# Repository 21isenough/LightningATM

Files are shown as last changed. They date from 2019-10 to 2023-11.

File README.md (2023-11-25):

# LightningATM

### 🔥🔥🔥 Now a seconde funding source next to LNbits is available. 🔥🔥🔥
### 👉👉👉 [blink.sv](https://www.blink.sv/) 🔥 See how to update: [Update](/docs/guide/perform_update.md) 👈👈👈

This LightningATM was built to distribute small amounts of BTC - obviously - it only accepts coins. It shall demonstrate the power of Bitcoins Lightning Network. A two cent coin is enough to buy some satoshis at the LightningATM.

A physical coin exchanged into bitcoin and send to your lightning wallet in seconds. Use this project to educate your family and friends or guests at your bitcoin meetup - a convenient and easy on-boarding process for people that are new to bitcoin.

**Please be aware that this is a hobbyist project and it is not secure and reliable enough to withstand attacks. I discourage the use of this setup in a professional environment - but it's rather a good educational tool**

There are currently two versions of the Lightning ATM. The large full version with a camera for scanning invoices and a button for acknowledgment and other functions. And there is the somewhat slimmed-down version for mobile use, the pocket version.

Full Version             |  Pocket Version
:-------------------------:|:-------------------------:
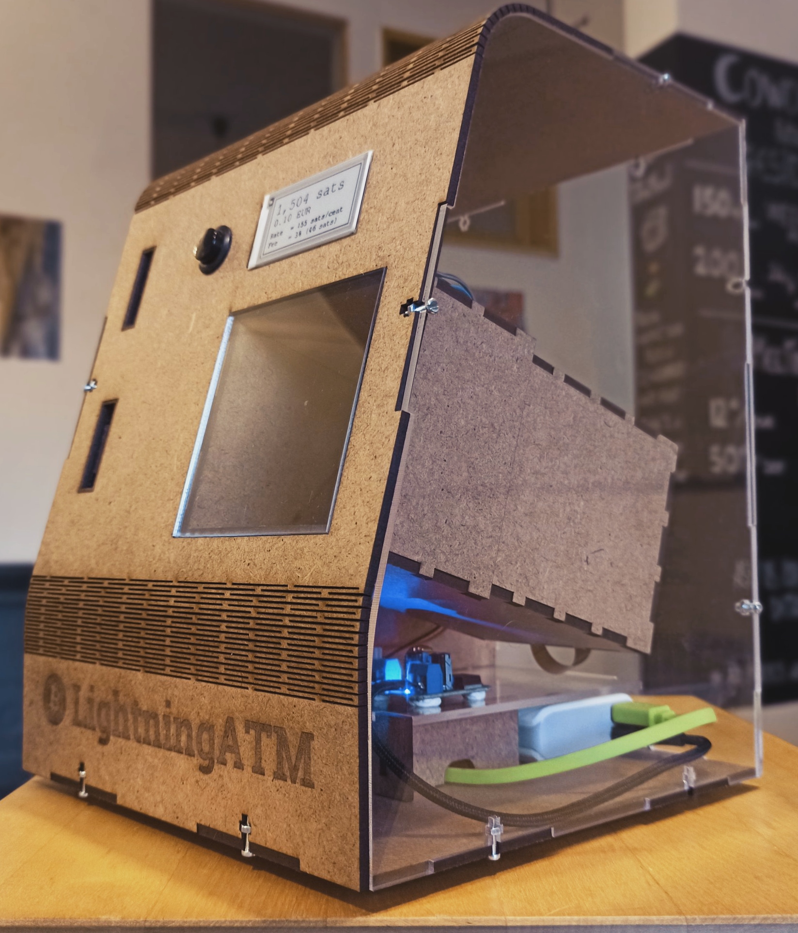
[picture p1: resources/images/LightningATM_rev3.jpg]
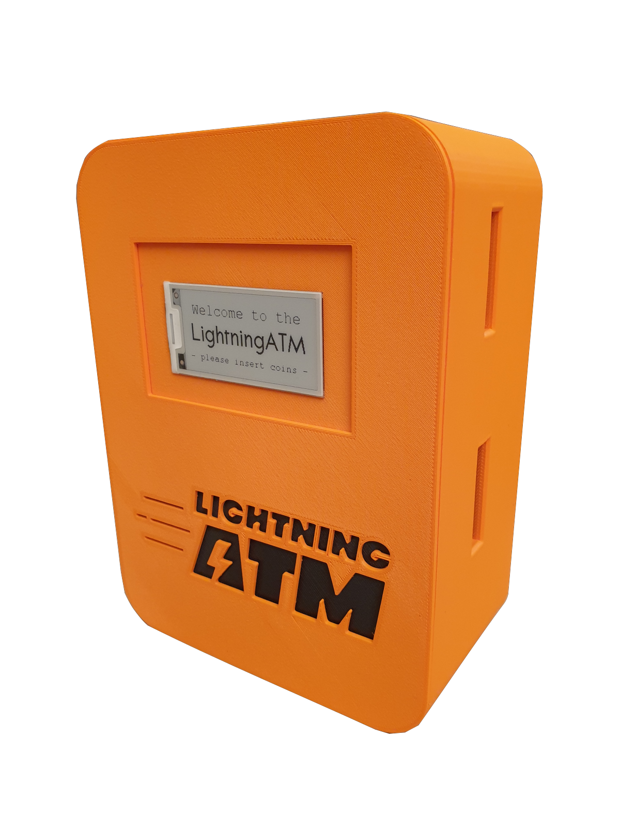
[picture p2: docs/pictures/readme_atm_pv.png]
  |  

### Required components

- [parts list](/docs/guide/parts_list.md)

### Installation guideline

_Carry out the points step by step as described here. This is the quickest way to succeed._ 😊

- [voltage converter](/docs/guide/voltage_converter.md)
- [coin validator](/docs/guide/coin_validator.md)
- [wiring](/docs/guide/wiring.md)
- [sd card and wifi](/docs/guide/sdcard_and_wifi.md)
- [display](/docs/guide/display.md)
- [edit config.ini](/docs/guide/edit_config.md)
- [debugging and tmux](/docs/guide/tmux_monitoring.md)
- [autostart](/docs/guide/autostart.md)
- [aditional information and tips](/docs/guide/information_and_tips.md)
- [option: language](/docs/guide/languages.md) 
- [option: button](/docs/guide/button.md)
- [option: camera](/docs/guide/camera.md)
- [option: lockout relay](/docs/guide/relay.md)
- [option: RPi image from scratch](/docs/guide/rpi_image_from_scratch.md)

If you want to update your ATM with LNbits, see this guide: [Update](/docs/guide/perform_update.md)

More information of how to setup the LightningATM can be found here https://docs.lightningatm.me. Also join the Telegram group of LightningATM builders here https://t.me/lightningatm_building or contact 21isenough on Twitter (https://twitter.com/21isenough).

To see the Lightning ATM in action, check out this video [LightningATM in action](https://twitter.com/21isenough/status/1170808396955738114?s=20)

### Mentioned
- https://podcasts.apple.com/us/podcast/interview-with-21isenough/id1481514734?i=1000458712983
- https://blog.sicksubroutine.com/lightning-junkies-episode-021/
- http://bitcoin-turm.de/bturm29/
- https://www.atmmarketplace.com/articles/lightning-atm-lets-you-buy-itty-bitty-amounts-of-bitcoin/
- https://www.bitcoinmedia.id/atm-bitcoin-lightning-ini-adalah-prototype-pertama/
- https://twitter.com/CoinATMRadar/status/1202657309765357568?s=20
- https://www.hackster.io/news/lightningatm-distributes-small-amounts-of-btc-over-the-lightning-network-5e03347acd88
- https://criptonizando.com/2019/10/08/desenvolvedor-cria-caixa-eletronico-de-bitcoin-que-ate-amadores-podem-construir-usando-a-lightning-network/
- https://decrypt.co/10046/ightningatm-how-to-make-your-own-bitcoin-atm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

### Documentations in other languages

- German Video: [Tutorial - Bitcoin Lightning ATM - montieren und konfigurieren](https://www.youtube.com/watch?v=pTyTc2qPQj0)
- German tutorial for the pocket edition: [Tutorial LightningATM - ereignishorizont.xyz](https://ereignishorizont.xyz/lightning-atm/)

### Todo list

#### Prio 1
- [ ] Implement lndconnect
- [ ] Add "no wallet setup" warning at boot
- [ ] Implement LNURLProxyAPI
- [ ] Support for more Lightning implementations and wallets
- [ ] Try different way of detecting inserted coins (populating a list and setting a delimiter)
- [ ] PCB Board design (https://easyeda.com/, http://kicad.org/)
- [ ] 5V-12V step up transformer (http://www.electronics-lab.com/project/5v-to-12v-step-up-dc-dc-converter/)
- [ ] Solve security concerns in regards to lnurl (scan over the shoulder)
#### Prio 2
- [ ] Dashboard for settings (via mobile)
- [ ] Add second button and admin menu
- [ ] Add admin function only available through qr pass
- [ ] Run certain functions in threads
- [ ] Additional button for restart and shutdown
- [ ] Find solution to work without jumper cables
- [ ] Add encrypted partition with sensible data
#### Prio 3
- [ ] Add TOR support for LND calls
- [ ] Store data in database
- [ ] Add AP option for users to login into their wifis (https://github.com/21isenough/RaspiWiFi)
- [ ] 2 layer for coins to reject before accepted
#### Done
- [X] Update doc with new features, screens
- [X] Check out BTCPay API to integrate backend
- [X] Add coin return stopper to 3d design
- [X] Try different e-ink screen
- [X] Add a language file to change strings easily
- [X] Write installations instructions (see docs.lightningatm.me)
- [X] Rethink the design decisions in regards to hardware (https://www.arrow.com/en/products)
- [X] Add encryption of admin.macaroon in idle mode
- [X] Design ideas for case
- [X] Slightly recline front board to the back, add immersion for camera
- [X] Move scanning function into utils
- [X] Move all display functions into display.py
- [X] Implement lnurl with lntxbot
- [X] Draw printer and boards in 3D (https://www.onshape.com/)
- [X] Write list of all compatible wallets/qr qr_codes
- [X] Test qr code on 2" eInk display (works)
- [X] Research camera resolutions / qr code scanning
- [X] Check if there's other zbar python libraries
- [X] Change to wide angle camera
- [X] Sort out scan errors
- [x] QR code scan function
- [x] Validate requested amount
- [x] Reject to high amounts
- [x] Add config file
- [x] Add parts list to readme
- [x] Ask for rescan of QR code
- [x] Inform about failed scan
- [x] Implement continuous QR Scan
- [x] Lower case ln invoices
- [x] Find a faster solution for QR scans (zbarcam)
- [x] Organize todos better

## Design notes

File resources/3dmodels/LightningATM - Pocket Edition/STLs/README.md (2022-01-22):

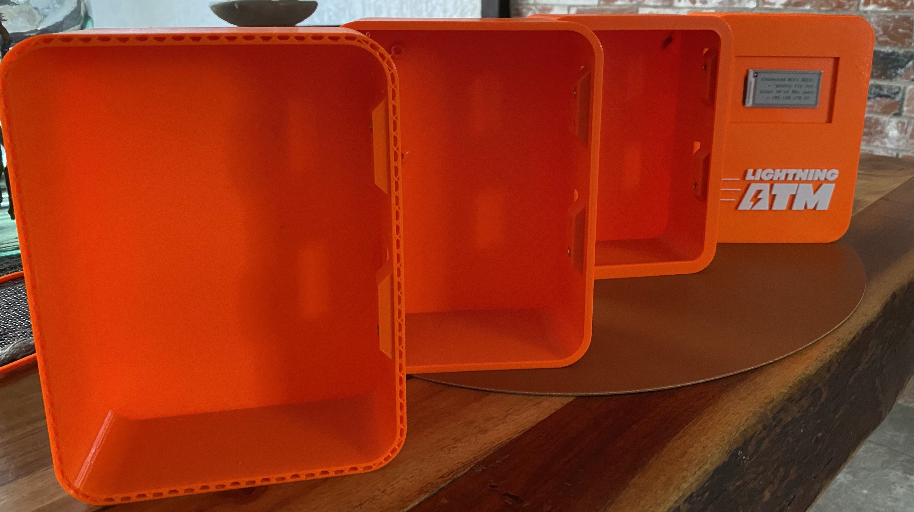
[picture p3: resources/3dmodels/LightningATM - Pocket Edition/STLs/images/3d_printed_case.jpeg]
 <br>

# 3D Printed L-ATM Case PE-Edition

Below files can be used to print a case, which lowers your overall costs. The models can be printed  without any supports.

This is the first version and is designed to be used with inserts to mount the Coin-Acceptor as well as the Rasbperry-Pi Zero. For the Coin Acceptor use **M3** inserts [(Amazon)](https://amzn.to/35eNkgj), for the Raspberry-Pi **M2.5** [(Amazon)](https://amzn.to/2HjF0Uo) inserts are needed.
The Lids holds by friction fit.

For the case **needed** are 3 Parts: 
- **Shell**
  
- **Back Lid**
  - two versions
    - normal with 2mm thick plate
    - thicker with 3mm thick plate
- **Top Lid**
  - there are two separate versions:
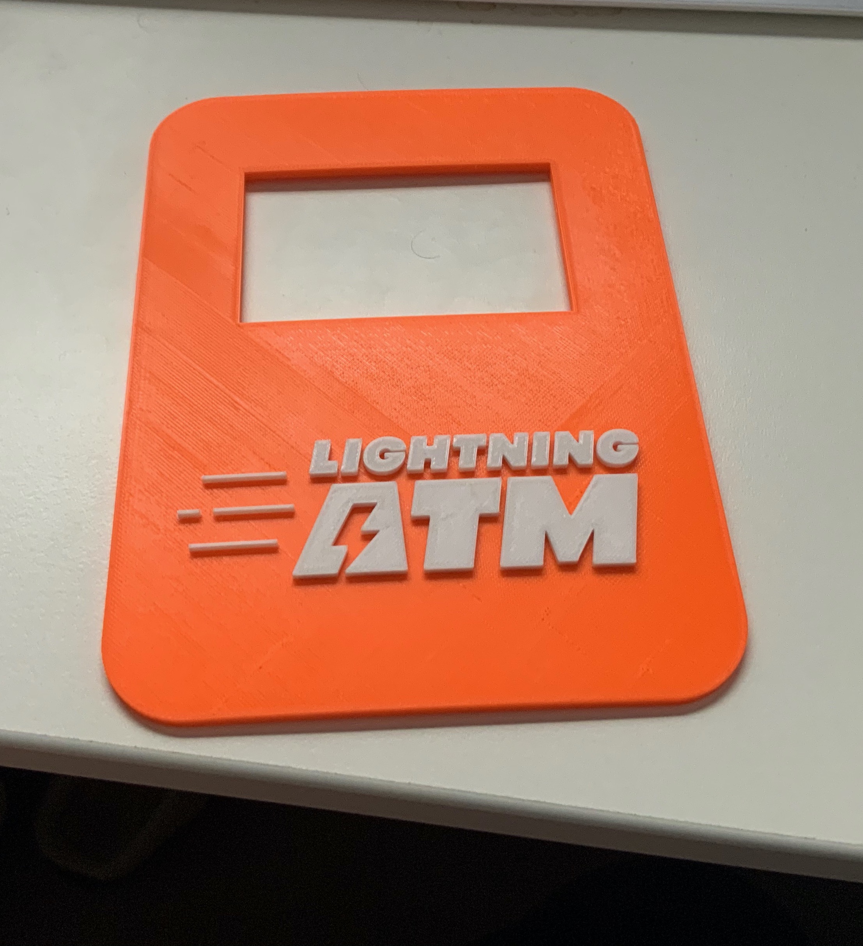
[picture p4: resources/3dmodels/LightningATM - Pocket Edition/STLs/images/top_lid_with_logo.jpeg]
    - with Lightning-Logo, *for dual color print add a **color change at Z 3.00 mm***. 
    - without any logo
- Mounting Rim
  - optional but *recommended* to properly glue the Top Lid onto the Back Lid.

1. Print Shell / Back Lid / Top Lid / Mounting Rim
2. Use soldering iron to:
   1. Add M3 Inserts into Coin Acceptor holes 
   2. Add M2.5 Inserts into Raspberry holes
   
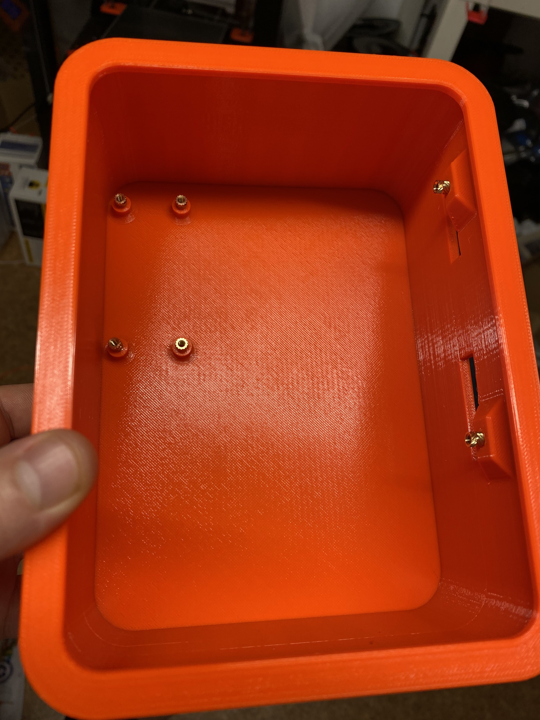
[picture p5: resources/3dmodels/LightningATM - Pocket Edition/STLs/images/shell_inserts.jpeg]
   <br> <br>
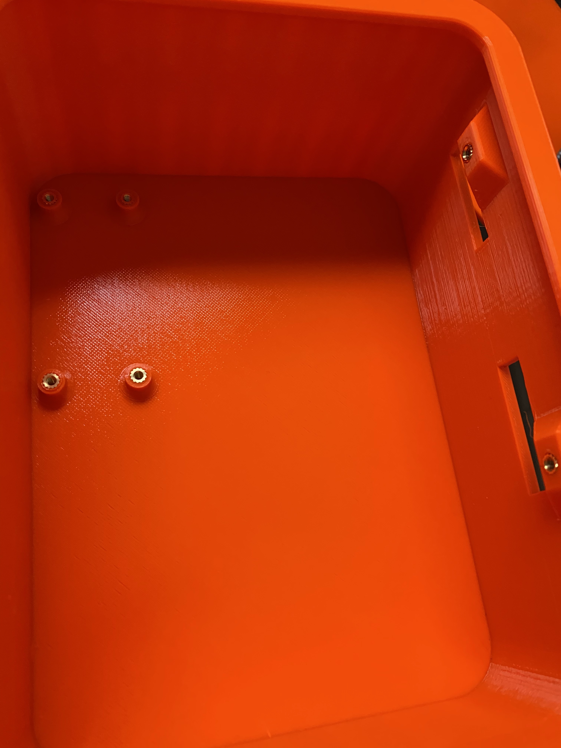
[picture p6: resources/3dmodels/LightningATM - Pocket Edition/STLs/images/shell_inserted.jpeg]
   
   
3. If you have printed the *Mounting Rim* put it around the BackLid
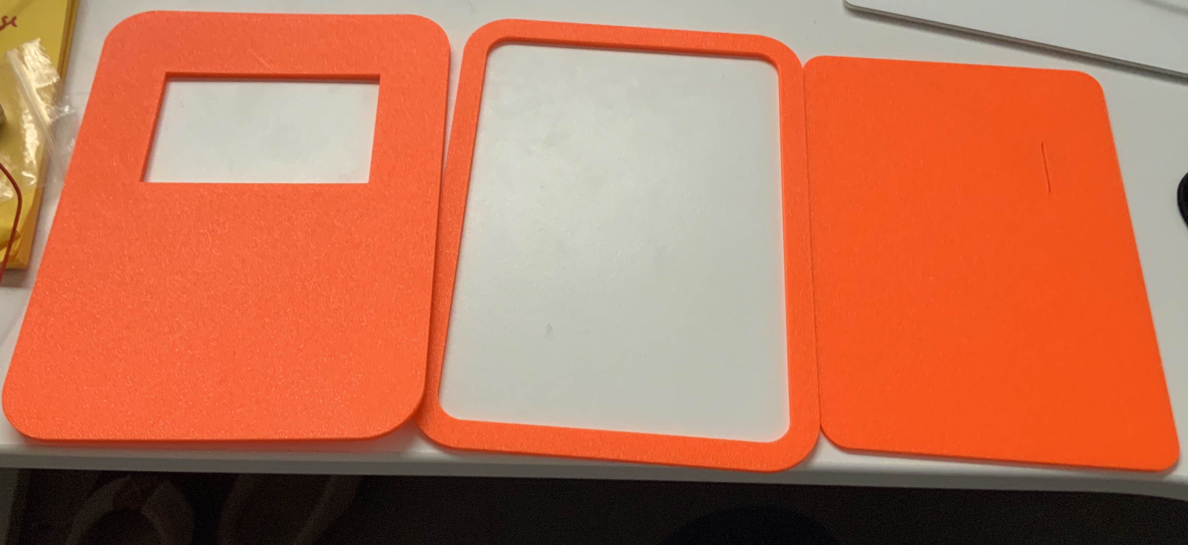
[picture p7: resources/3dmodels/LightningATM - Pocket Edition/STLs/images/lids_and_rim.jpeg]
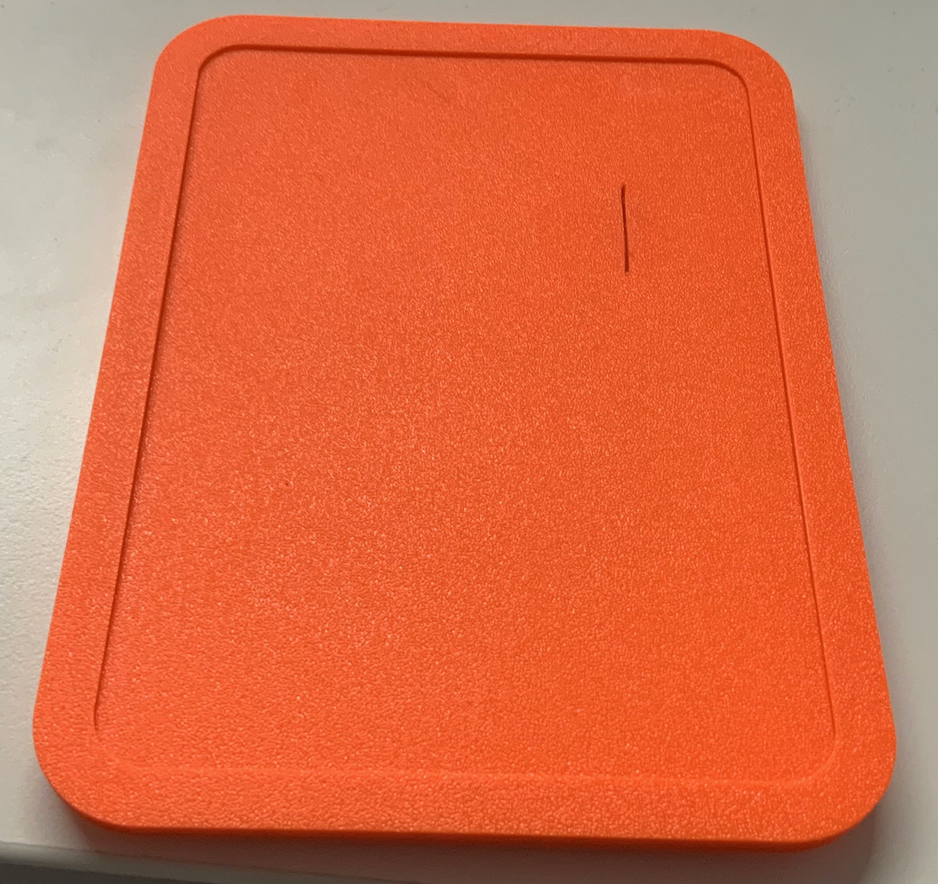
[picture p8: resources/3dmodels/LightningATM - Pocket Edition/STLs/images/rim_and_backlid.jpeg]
<br> <br> 
4. put glue on the Top Lid and use something to press both together
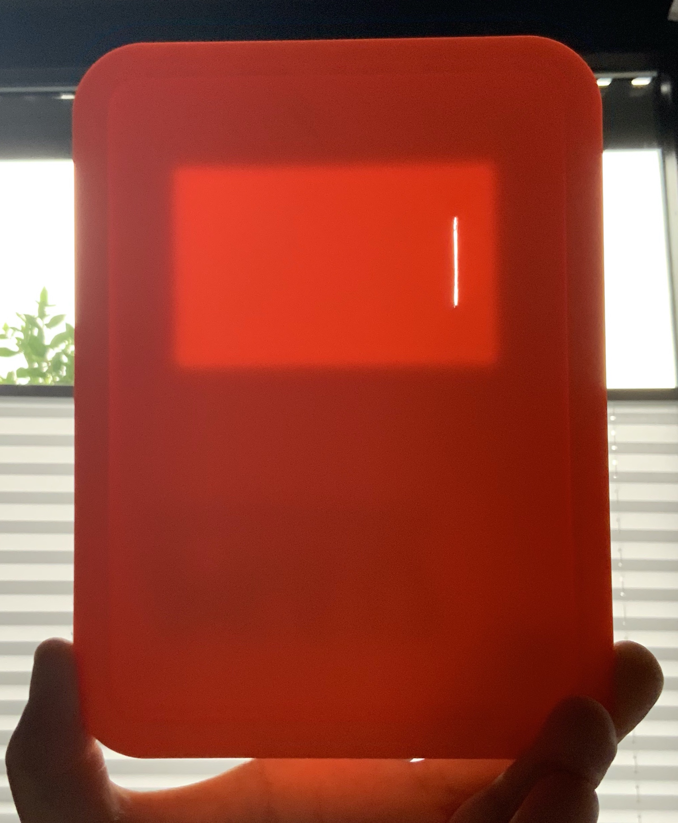
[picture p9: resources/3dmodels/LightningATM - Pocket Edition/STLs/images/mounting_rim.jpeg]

5. this is what it should look like without the rim
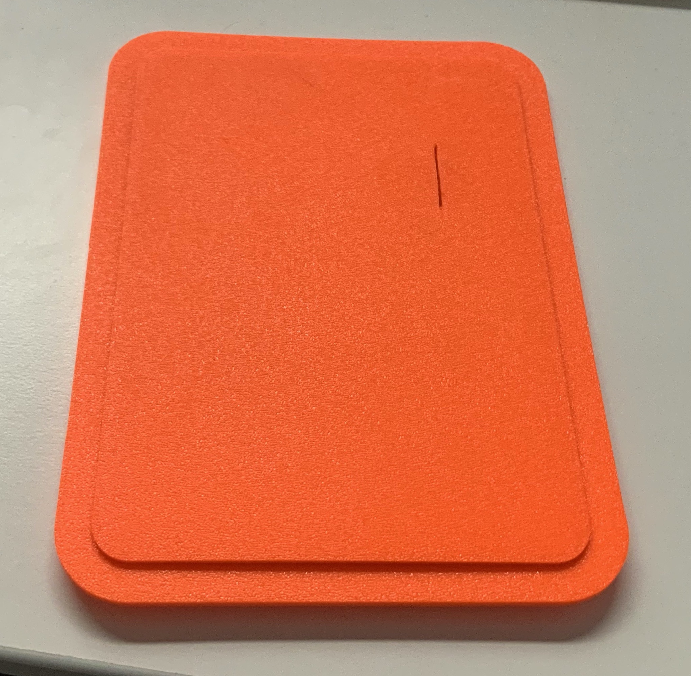
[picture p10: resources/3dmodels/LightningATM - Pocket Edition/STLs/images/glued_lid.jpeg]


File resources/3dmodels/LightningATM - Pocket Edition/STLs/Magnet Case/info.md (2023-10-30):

I have added new 3D models, which can be supplemented with magnets so that you no longer have to attach the front panel to the case with a rubber band. You can find the procedure and more details in my Twitter Thread ...

Magnets: 5x5mm round nickel plate: https://www.supermagnete.ch/scheibenmagnete-neodym/scheibenmagnet-5mm-5mm_S-05-05-N
Metal plates: 2x10mm self-adhesive: https://www.supermagnete.ch/magnethaftgruende-selbstklebend/metallscheiben-selbstklebend-10mm_PAS-10

For more information please DM me on Twitter or Telegram! @Nicolas_b58

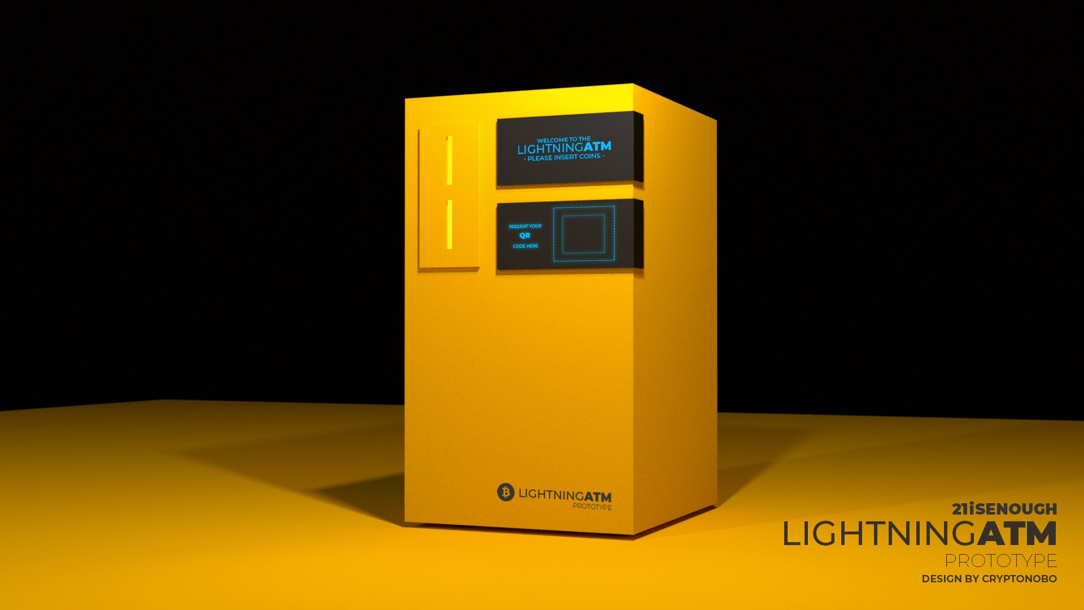
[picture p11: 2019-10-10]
resources/images/LightningATM_design_by_@cryptonobo.jpeg

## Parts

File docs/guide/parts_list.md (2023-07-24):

## Parts list

- Raspberry Pi Zero W* / supported alternatives:

    - Raspberry Pi Zero WH (best option, with populated header) [link](https://www.google.com/search?q=Raspberry+Pi+Zero+WH) 
    - Raspberry Pi Zero W (without header, you have to solder a header) [link](https://www.google.com/search?q=Raspberry+Pi+Zero+W) 
    - Raspberry Pi Zero 2 W (possible, but you have to create an image from [scratch](/docs/guide/rpi_image_from_scratch.md)) [link](https://www.google.com/search?q=Raspberry+Pi+Zero+2+W) 

- Micro SD Card (16 - 64 GB tested) [link](https://www.google.com/search?q=Micro+SD+Card) 
- DC-DC Adjustable Step Up Power Module (5V->12V) e.g. [LM2587S](https://www.ebay.de/itm/DC-DC-Adjustable-Step-up-Boost-Power-Supply-LM2587S-3V-5V-12V-to-19V-24V-30V-36V-/402196830271) or [HW-637](https://www.amazon.de/Converter-verstellbar-Spannungsregler-Effizienz-Board-Green-1-gr%C3%BCn/dp/B07S5YH2MB)
- Multi Coin Acceptor (programmable, e.g. [Coin Acceptor 616](https://www.google.com/search?q=Coin+Acceptor+616) or [this](https://de.aliexpress.com/item/1005002636710497.html))
- Display with HAT / supported alternatives:

    - PaPiRus Zero 2.0 "- ePaper pHAT 
    - Inky pHAT 2.13inch ePaper/eInk/EPD 
    - Waveshare 2.13inch e-Paper HAT [link](https://www.waveshare.com/wiki/2.13inch_e-Paper_HAT) 
    - Waveshare 2.13inch e-Paper HAT (D) [link](https://www.waveshare.com/2.13inch-e-paper-hat-d.htm) (Recommendation for Pocket Edition!)
    - Waveshare 2.66inch e-Paper E-Ink Display Module + [HAT](https://www.waveshare.com/wiki/E-Paper_Driver_HAT) 
    - Waveshare 2.7inch E-Ink display HAT [link](https://www.waveshare.com/wiki/2.7inch_e-Paper_HAT)

- Micro USB cable [link](https://www.google.com/search?q=usb+2+micro+b) 
- Jumper cable [link](https://www.google.com/search?q=jumper+cable)
- A good USB power supply. Power adapter or power pack with 2 amps.

### Opitional parts

- Push Button (Recommended option!). Optionally with LED (3V) e.g. this [example](https://www.amazon.de/dp/B00UFNI47I/). For the LED you will also need a resistor. 
- Lockout Relay Module (Makes sense!) e.g. [HW-482](https://www.google.com/search?q=HW-482) or [KY-019](https://www.google.com/search?q=KY-019) 
- Raspberry Pi Camera 5MP OV5647 
- ATM Case (self printing [DXF files](https://github.com/21isenough/LightningATM/tree/master/resources/3dmodels) or [STL files for Pocket Edition](https://github.com/21isenough/LightningATM/tree/master/resources/3dmodels/LightningATM%20-%20Pocket%20Edition/STLs) plus [threaded insert](https://www.google.com/search?q=threaded+insert) or buy from [Fulmo](https://shop.fulmo.org/shop/))

### Alternative a total construction set for the Pocket Edition from [Fulmo](https://shop.fulmo.org/product/the-lightning-atm-bitcoin-construction-set/)

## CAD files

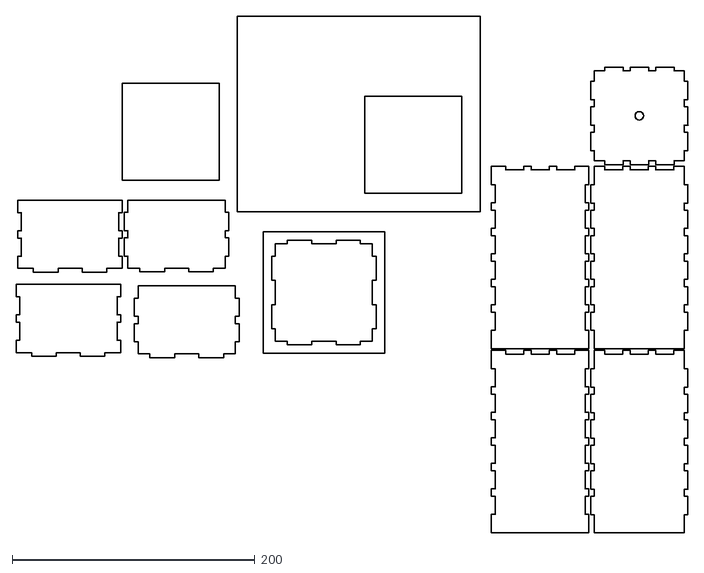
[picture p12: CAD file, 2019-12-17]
resources/3dmodels/Compartments.dxf
553.5 x 425.6

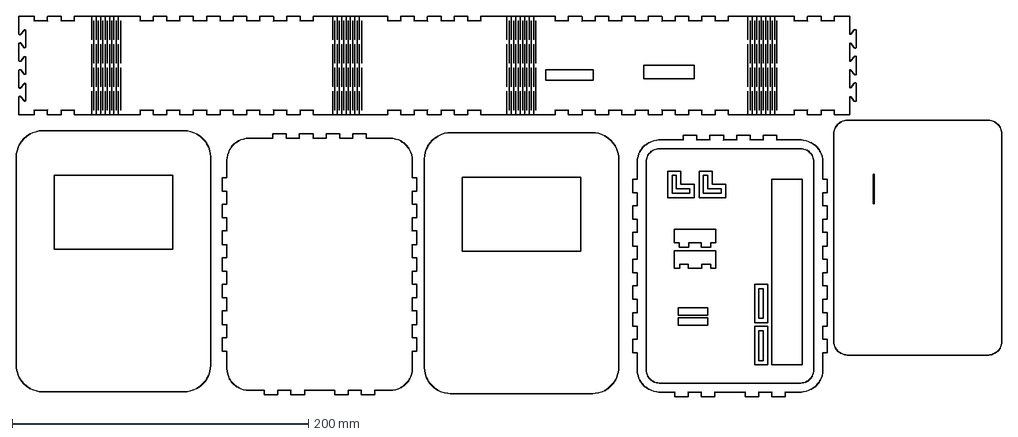
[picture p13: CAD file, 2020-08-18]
resources/3dmodels/LightningATM - Pocket Edition/LightningATM Pocket Edition - V0.1 - MDF - 3mm.dxf
665.2 x 256.5 mm

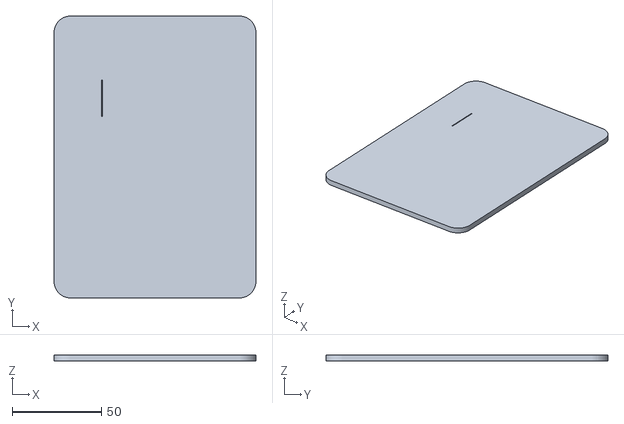
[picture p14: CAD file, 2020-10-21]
resources/3dmodels/LightningATM - Pocket Edition/STLs/Back_Lid_THICKER_v1_NoSupp.stl
113.4 x 158.4 x 3.50

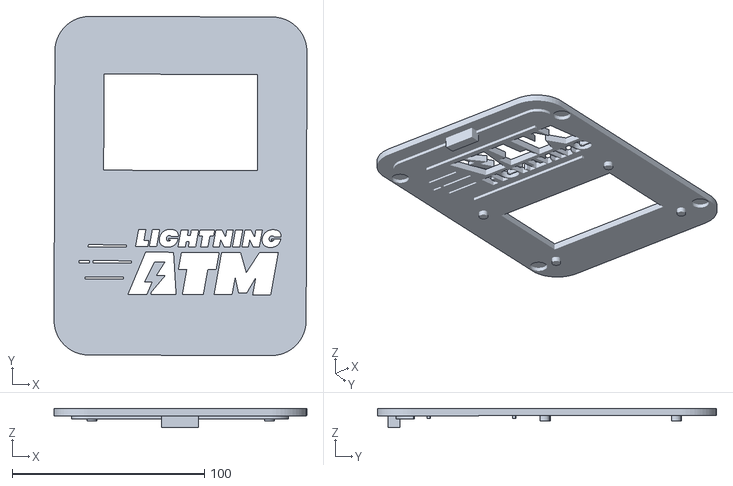
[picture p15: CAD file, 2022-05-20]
resources/3dmodels/LightningATM - Pocket Edition/STLs/Magnet Case/Front Magnet.stl
131.6 x 176.5 x 9.99

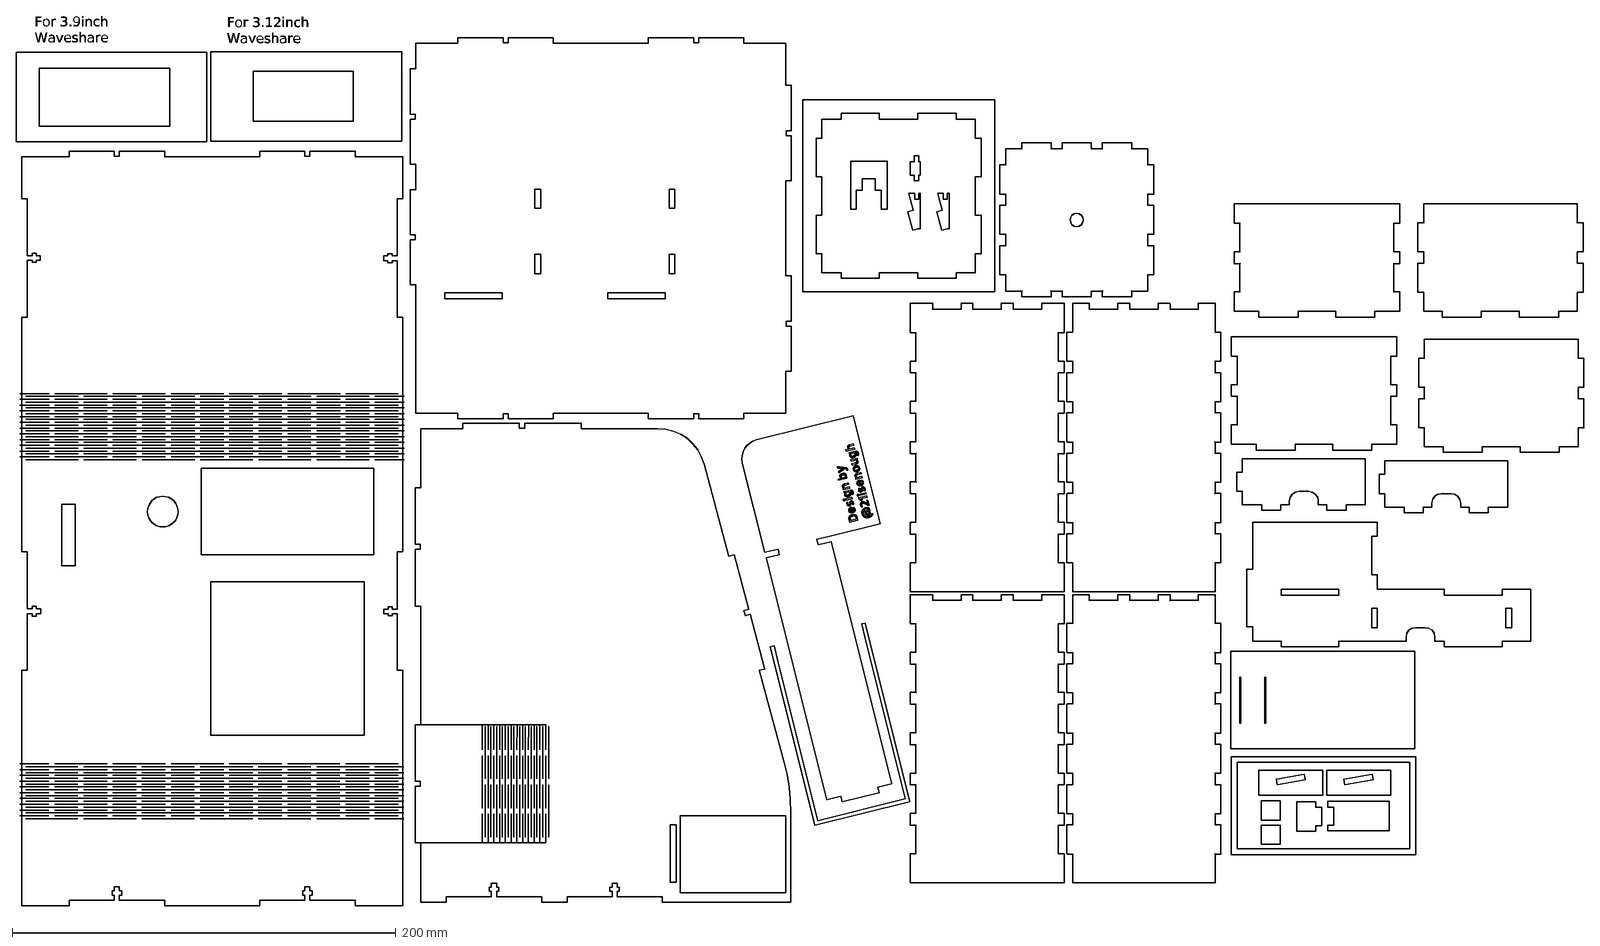
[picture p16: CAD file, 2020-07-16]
resources/3dmodels/LightningATM/LightningATM - V0.4 - MDF - 3mm.dxf
For 3.9inch Waveshare
For 3.12inch Waveshare

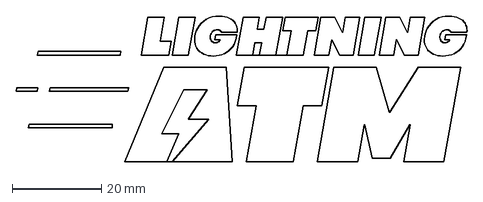
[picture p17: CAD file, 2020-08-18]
resources/3dmodels/LightningATM - Pocket Edition/LightningATM Pocket Edition - V0.1 - Engraving.dxf
100.9 x 32.6 mm

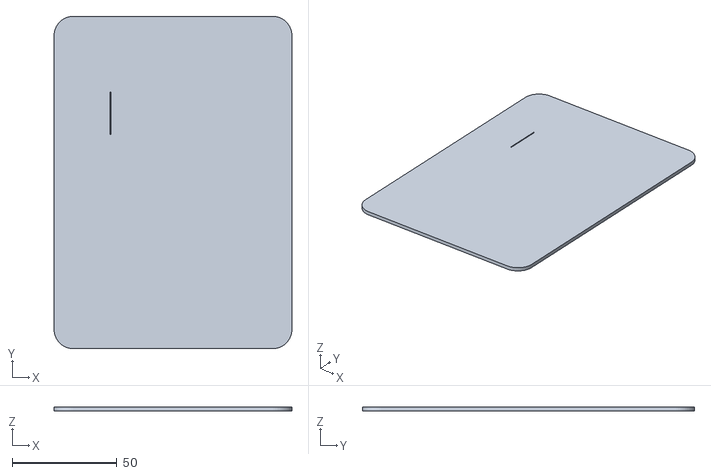
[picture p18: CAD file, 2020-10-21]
resources/3dmodels/LightningATM - Pocket Edition/STLs/Back_Lid_NORMAL_v1_NoSupp.stl
113.4 x 158.4 x 2.00

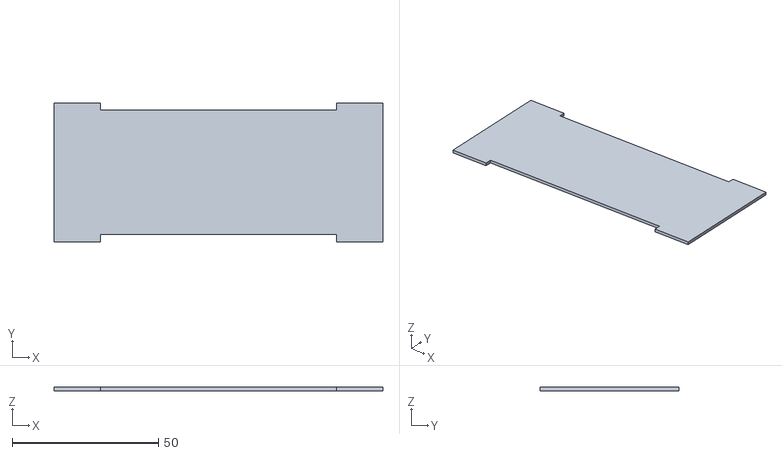
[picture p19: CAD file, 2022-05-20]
resources/3dmodels/LightningATM - Pocket Edition/STLs/Magnet Case/Logo Backplate Magnet.stl
112.3 x 47.6 x 1.20

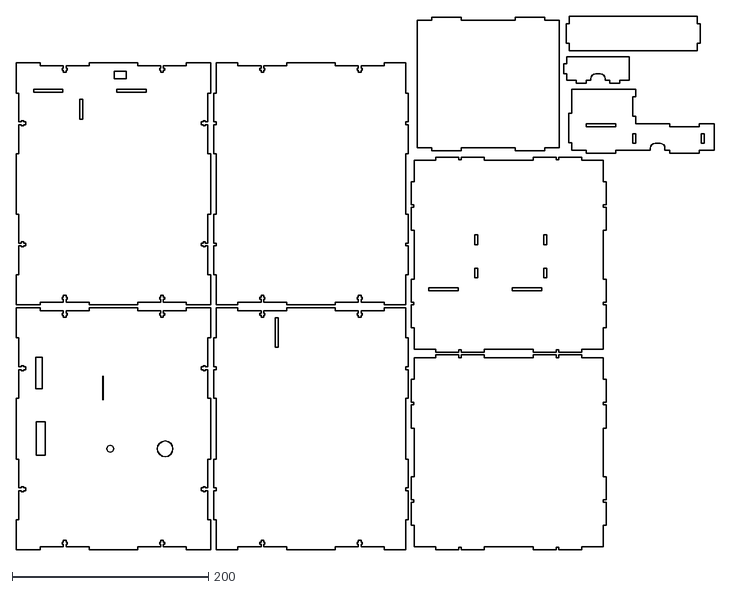
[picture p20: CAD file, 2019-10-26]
resources/3dmodels/LightningATM - Sketch.dxf
711.4 x 543.8

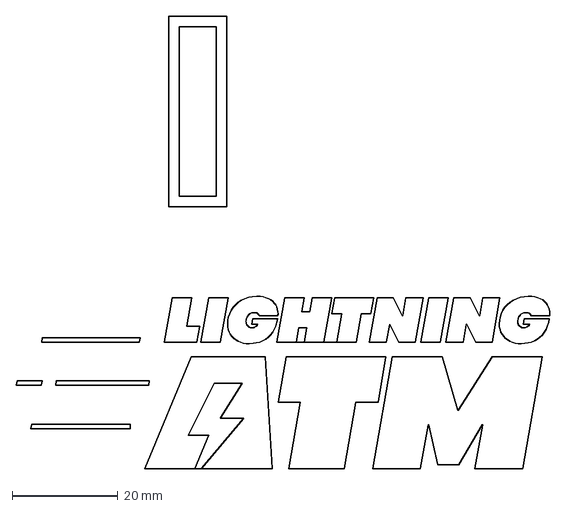
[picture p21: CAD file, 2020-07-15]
resources/3dmodels/LightningATM/LightningATM - V0.4 - Engraving.dxf
100.9 x 85.6 mm

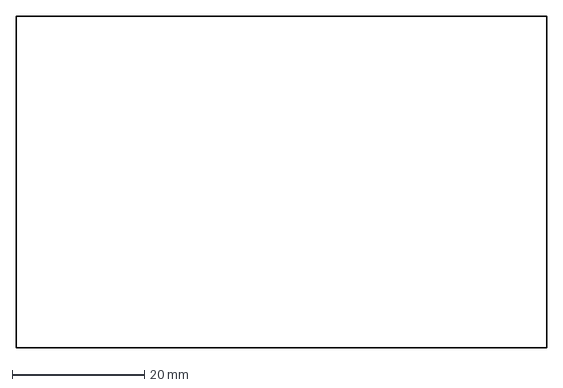
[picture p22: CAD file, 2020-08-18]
resources/3dmodels/LightningATM - Pocket Edition/LightningATM Pocket Edition - V0.1 - Acrylic - 3mm.dxf
80.2 x 50.2 mm

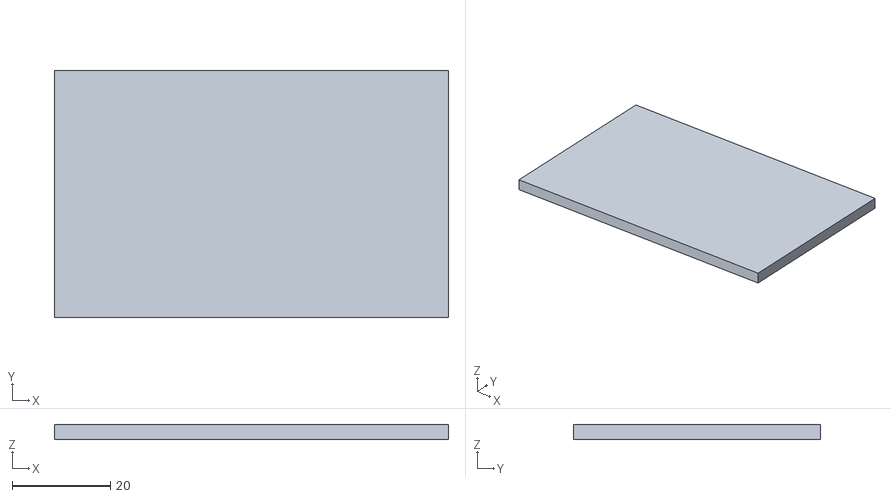
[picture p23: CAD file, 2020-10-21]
resources/3dmodels/LightningATM - Pocket Edition/STLs/Front_Glass_v1_NoSupp.stl
80.2 x 50.2 x 3.00

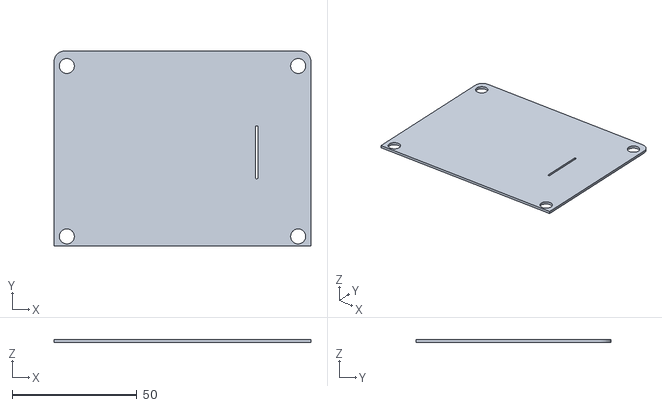
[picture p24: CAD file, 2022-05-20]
resources/3dmodels/LightningATM - Pocket Edition/STLs/Magnet Case/Screen Backplate Magnet.stl
103.0 x 78.1 x 1.20

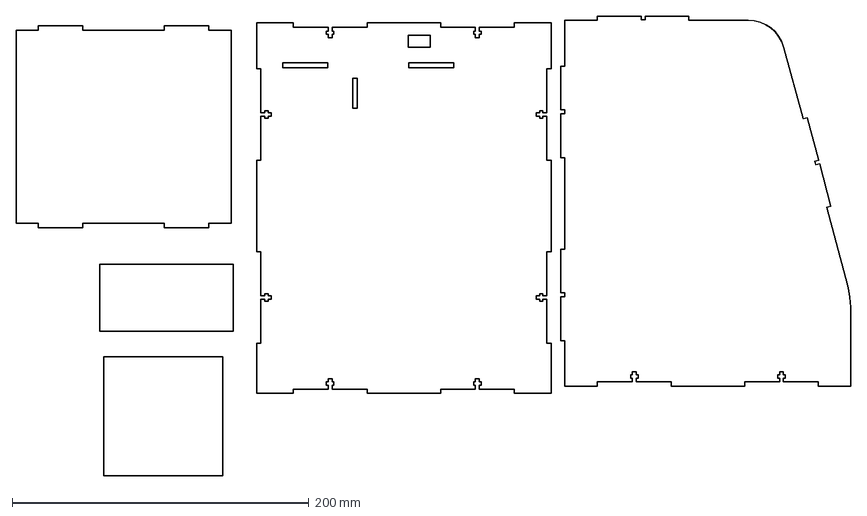
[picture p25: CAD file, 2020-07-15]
resources/3dmodels/LightningATM/LightningATM - V0.4 - Acrylic - 3mm.dxf
562.8 x 310.1 mm

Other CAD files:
resources/3dmodels/LightningATM - Pocket Edition/STLs/Magnet Case/Case Magnet.stl
resources/3dmodels/LightningATM - Pocket Edition/STLs/Shell_v1_NoSupp.stl
resources/3dmodels/LightningATM - Pocket Edition/STLs/Top_Lid_with_Logo_v1_NoSupp.stl
resources/3dmodels/LightningATM - Pocket Edition/STLs/just_logo.stl
resources/3dmodels/LightningATM - Pocket Edition/STLs/Top_Lid_No_Logo_v1_NoSupp.stl
resources/3dmodels/LightningATM - Pocket Edition/STLs/optional_Mounting_Rim_v1_NoSupp.stl
resources/3dmodels/LightningATM/old_versions/LightningATM - V0.1 - final laser layout.dxf
resources/3dmodels/LightningATM/old_versions/LightningATM - V0.1.dxf
resources/3dmodels/LightningATM/old_versions/LightningATM - V0.2 - Acrylic.dxf
resources/3dmodels/LightningATM/old_versions/LightningATM - V0.2 - Engraving.dxf
resources/3dmodels/LightningATM/old_versions/LightningATM - V0.2 - MDF.dxf
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

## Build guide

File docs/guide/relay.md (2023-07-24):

# Coin acceptor lockout relay / electromagnetism gate

## The electromagnetic gate 

The electromagnetic gate is a blocking pin that diverts the coins to the ejection. When the coin validator is de-energized, the pin always remains locked and ejects all coins. The blocking pin is only pulled back by a magnetic coil when the coins are correctly recognized. Only then do the coins fall through into fiat hell. This electromagnetic gate can be controlled or blocked from outside. The function can be used to exclude multiple impulses (in the case of fast coin insertion in a row) or coin insertion during a certain period of time (a display reading or with AMT offline).

## There are two ways to lock the electromagnetic gate

1. Via the "SET" input on the ATM. It is always "open / not connected" by default. The electromagnetic gate is only locked when these two contacts are short-circuited, or released when the contact is opened / not connected again.
2. The interruption of the coil control. To do this, however, you have to cut open the line and put a clamp in between so that you can loop in a contact there.

Relay options

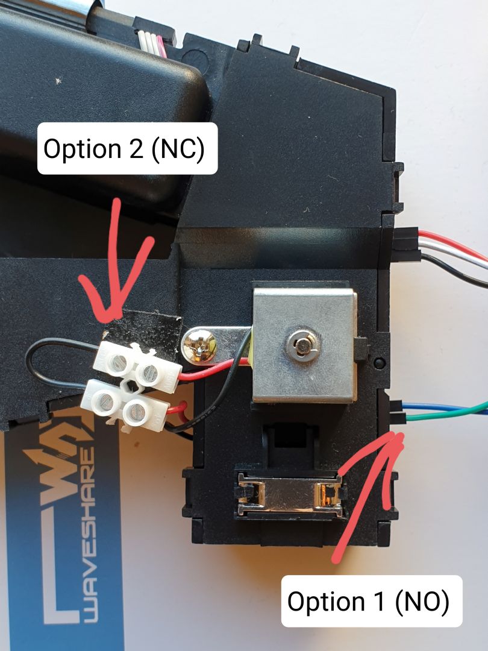
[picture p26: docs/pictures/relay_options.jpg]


Which option you choose is up to you. Option 1 is certainly the easiest. However, plugging in the cables can prove difficult. I finally decided on option 2 because the clamp connection seemed more stable than the plug connection. But it doesn't matter which variant you choose, you just have to make sure that you use the opener or the closer contact. 

## The Relay Module

A potential-free contact is required to switch the contact for the coin checker. A relay module with a changeover contact is ideal here.

Relay           |  build in
:-------------------------:|:-------------------------:
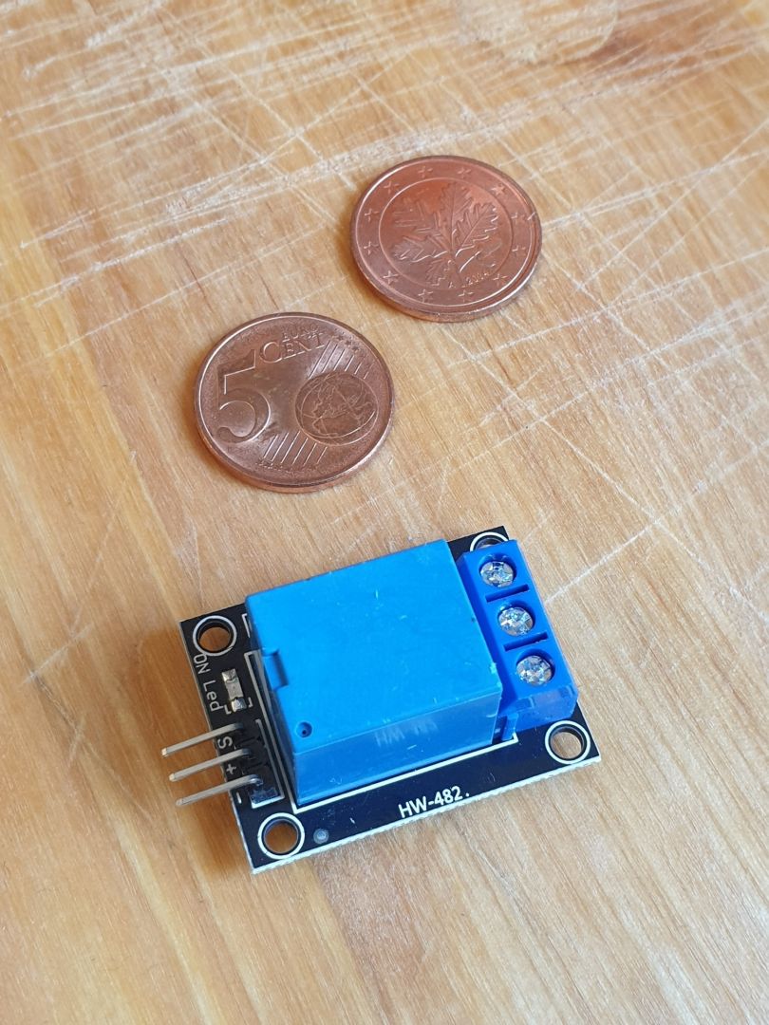
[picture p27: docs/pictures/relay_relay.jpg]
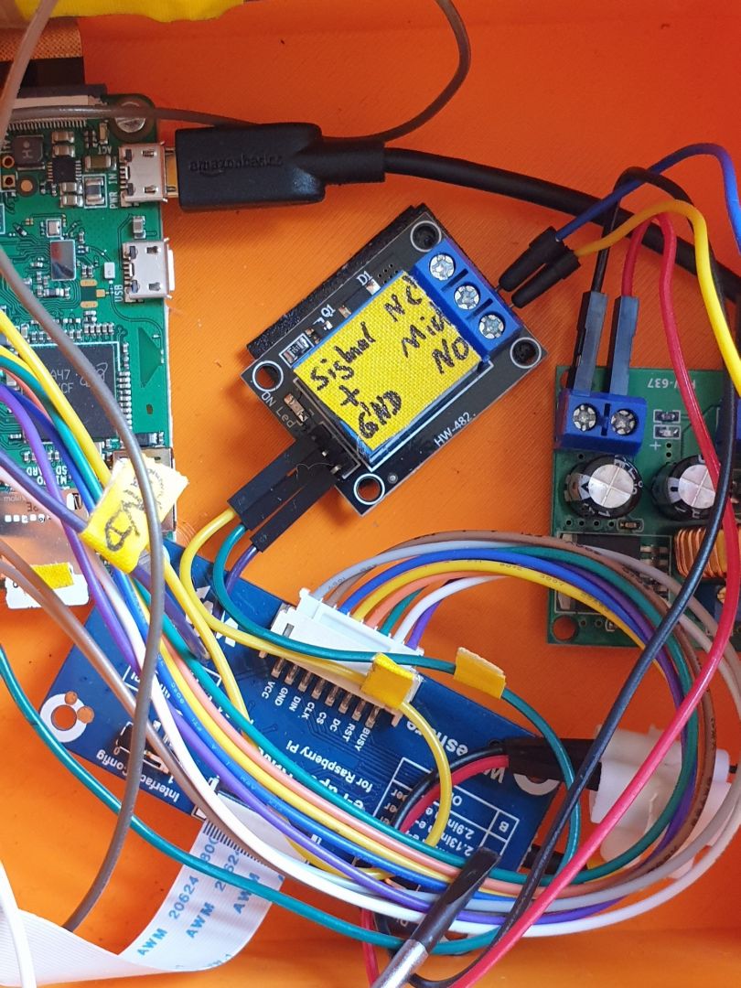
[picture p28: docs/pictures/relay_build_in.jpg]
  |  

For a special typ, see [parts_list](/docs/guide/parts_list.md).

## Wiring

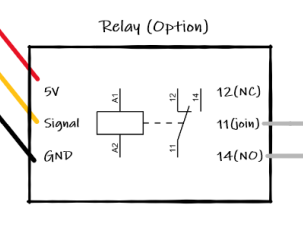
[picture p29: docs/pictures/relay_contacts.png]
You can find the contacts / wiring for the relay here  and in total [here](/docs/guide/wiring.md).

When the relay is not energized, terminal 11 is the common contact and the contact to terminal 14 is open (NO = normal open). Terminal 12 is closed when unswitched (NC = normal close). If the coin acceptor is "released", then the whole thing is reversed.

## Relay Test

If you want to test the relay, we have a small test program here. It toggles the relay on and off alternately every two seconds. After starting the ATM, log in to the AMT via SSH and gradually enter the following command, similar to the button and LED tests in the [button](/docs/guide/button.md) chapter.

```
	$ sudo systemctl stop LightningATM.service
	$ cd ~/LightningATM/tests
	$ sudo python3 relay_test.py
	$ sudo systemctl start LightningATM.service
```

Relay test

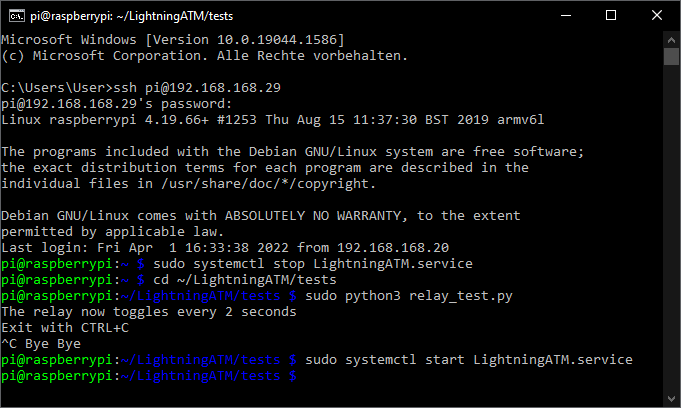
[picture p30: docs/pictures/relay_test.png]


## The result

Once everything has been wired and is back in operation, you should notice the following:

1. ATM power off: All coins are ejected.
2. ATM Ready: Coins are accepted.
3. Coin inserted: Relay switches for a short time and ejects all new coins immediately. Only when the display has updated is the coin validator released again.
4. The ATM shows the QR code: The coin validator is blocked, the coins are ejected.
5. You have a different display than the start display (selection for versions with a button): The coin validator is blocked.
6. The ATM is out of service: The coin validator is blocked.

If the ATM is ready but does not accept the coins, then check whether the relay switches is on (see LED) after the AMT has started up. If the relay works an you still can't insert coins, swap the terminals 12 and 14.

---

#### [option: camera](/docs/guide/camera.md)  ᐊ  previous | next  ᐅ  [option: RPi image from scratch](/docs/guide/rpi_image_from_scratch.md)

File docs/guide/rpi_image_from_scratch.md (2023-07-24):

## Raspberry Pi image from scratch

### For example for the RPi Zero 2 or using new version of Raspibian as Bullseye in any other RPi.

#### `Warning:` It is not recommended to use the RPi Zero 2 for the Lightning ATM. However, if you already have one, you can use this guide to get it working. 

The Raspberry Pi Zero 2 is not supported in the Raspberry "Stretch" version. The tried and tested "2019-04-08-raspbian-stretch-lightningatm.gz" image does not run on the Zero 2. Accordingly, a new image must be created that supports the RPi Zero 2. The current [Bullseye](https://en.wikipedia.org/wiki/Raspberry_Pi_OS) version (32-bit) does this. You can use Bullseye image, but still needs to be modified so that it can be used for the Lightning ATM.

Unfortunately, Bullseye does not support all components directly. The Waveshare displays are direct compatible and for the PaPiRus displays you have to install the library. 
  
This is only a guide for creating a compatible version. Deviations are possible and maybe even necessary. For the best result, however, it is recommended to stick to the procedure. Otherwise, troubleshooting support will be difficult. Since this is an experimental setting, any guarantee or warranty is excluded.
  
### The individual steps:

1. Download and burn the raw image
2. Add SSH, userconf and Wifi data to the raw image
3. First start and first settings
4. Option: Install PaPiRus display library 
5. Carry out updates and installations
6. Install and test the display
7. Create and edit the config.ini
8. Postprocessing

---

### 1. Download and burn the raw image

Find the appropriate Raspberry Pi OS (32-bit) image from the raspberrypi.org [Archive](https://downloads.raspberrypi.org/raspios_armhf/images/) and download it. You can use a newer version, but the "2022-01-28-raspios-bullseye-armhf.zip" version was tested for this tutorial. Unpack the file and write the image with [balenaEtcher](https://www.balena.io/etcher/). When done, remove the microSD.

### 2. Add SSH, userconf and Wifi data to the raw image

- Create an empty file named `SSH` in preparation. Make sure that the file has __no__ file extension such as `.txt`. It is just called `SSH` and will later activate the SSH connection on the Raspberry Pi.
- Create a `wpa_supplicant.conf` file as described in chapter [sd card and wifi](/docs/guide/sdcard_and_wifi.md). This gives the Raspberry Pi the necessary information about your Wifi.
- Create a file named `userconf` with __no__ file extension and add the next content:
	```
	pi:$6$AkXCaGAo9kHlKdQS$FOsYUzv6Ypm/QEw78HBidWQtT1n83T4IsQcmDsWdOfZDgHTd1HUoVT6c3VZ6WDHC36/OHt380mIFiMyHlAU8A/
	```
	This content sets the password for the `pi` user to `password`. In newer versions as Bullseye the default password is not set automatically so we need to make this step.
- Put the newly written microSD back into the computer slot and copy the three files into the "boot" directory.
- Remove the microSD. It is now ready for the Raspberry Pi.

### 3. First start and first settings

After starting the Zero 2 and waiting a few minutes. Then you can log in as described in the [sd card and wifi](/docs/guide/sdcard_and_wifi.md) chapter.

- Change the password and remember it!

		$ passwd
		
-   Activate the SPI interface for the display.

		$ sudo raspi-config

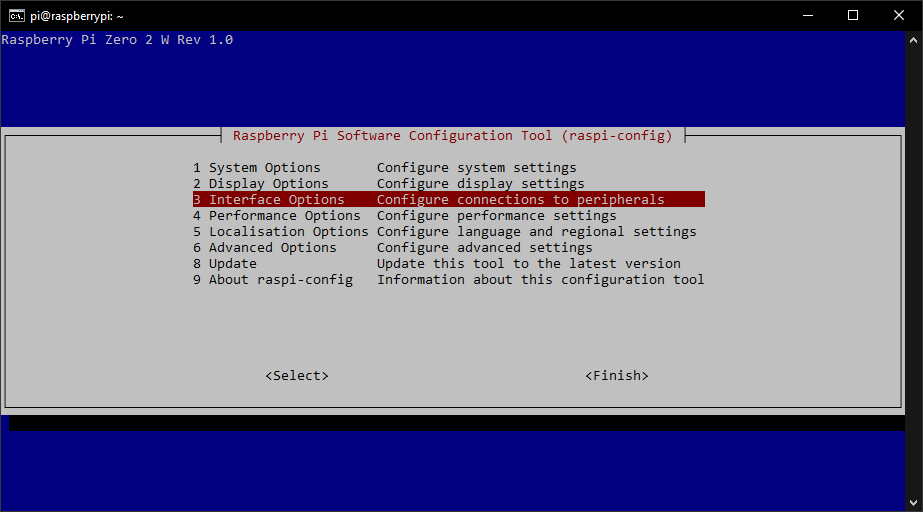
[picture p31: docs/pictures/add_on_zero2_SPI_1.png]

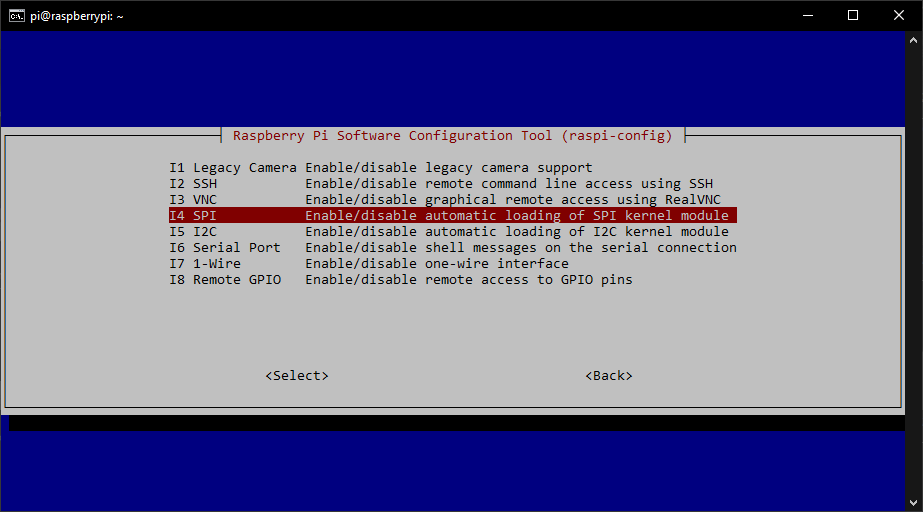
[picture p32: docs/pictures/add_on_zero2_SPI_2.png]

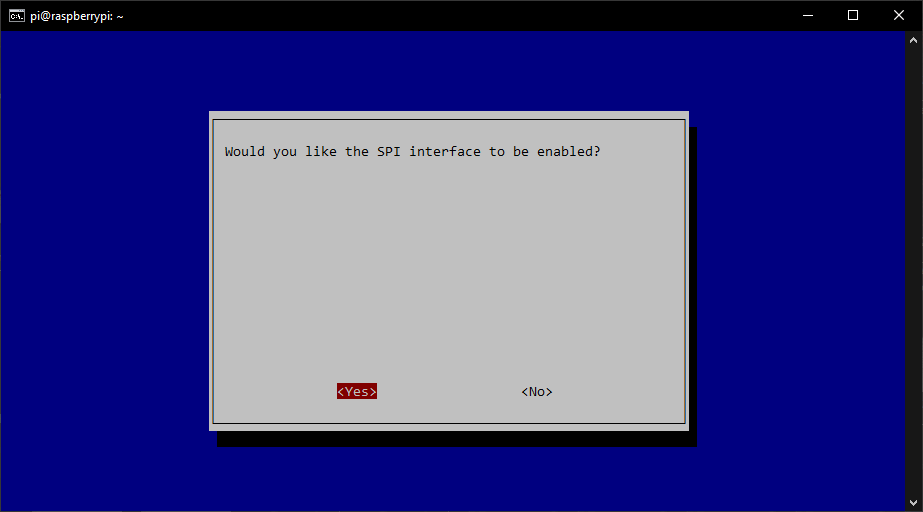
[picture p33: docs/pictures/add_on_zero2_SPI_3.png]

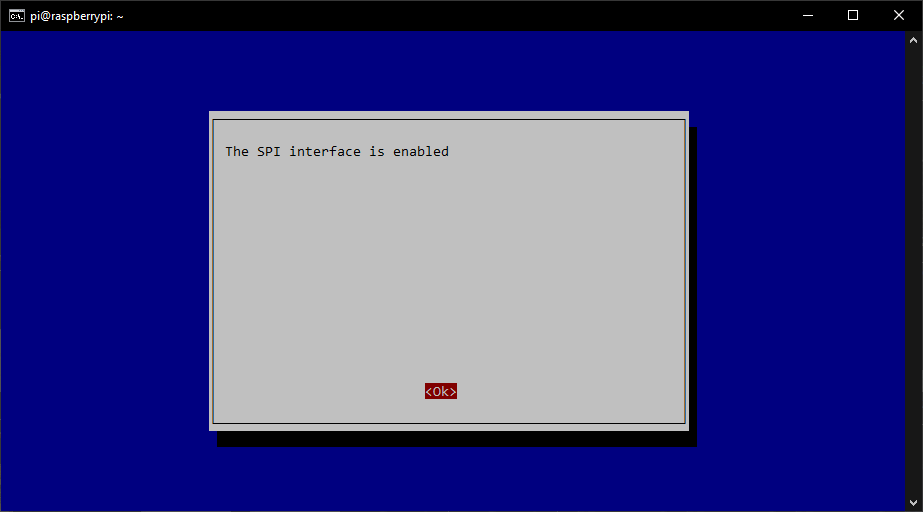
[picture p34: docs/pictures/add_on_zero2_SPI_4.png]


- Exit with "Finish".

### 4. Option: Install PaPiRus display library 

If you use a PaPiRus Display, you have to install the PaPiRus display library. If you have a Waveshare or other, you can cancel this step.

	$ curl -sSL https://pisupp.ly/papiruscode | sudo bash

Set it to Python 3

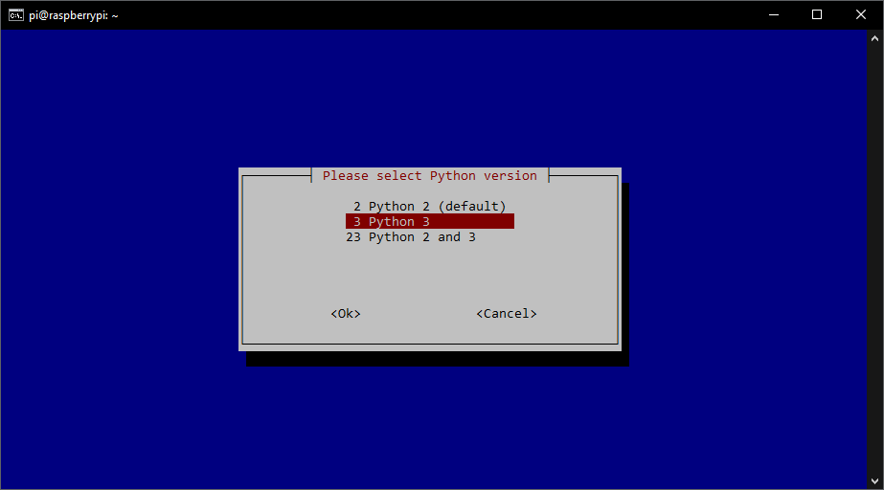
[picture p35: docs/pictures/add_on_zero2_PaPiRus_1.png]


Choose your display size

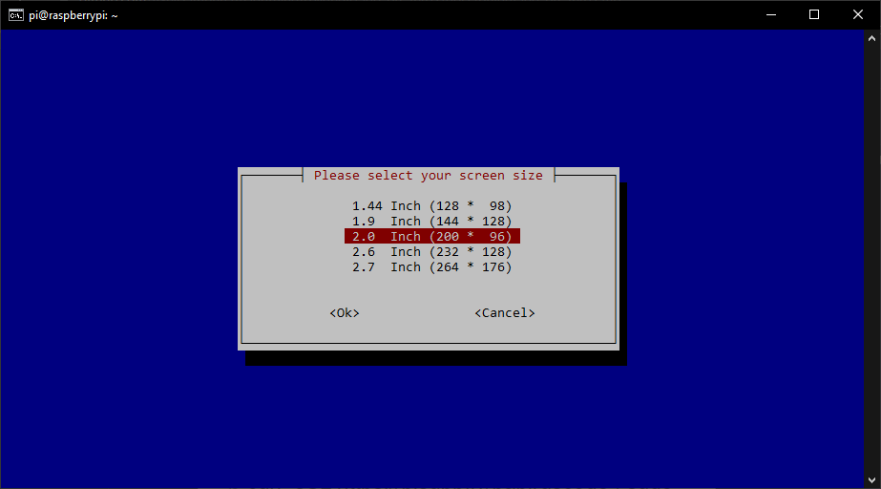
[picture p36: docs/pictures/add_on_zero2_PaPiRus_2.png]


### 5. Carry out updates and installations

It's the same like described in chapter [sdcard_and_wifi](/docs/guide/sdcard_and_wifi.md). Run the following commands one by one.

```
	$ sudo apt update && sudo apt upgrade
	$ git clone https://github.com/21isenough/LightningATM.git
	$ cd ~/LightningATM/
	$ pip3 install -r requirements.txt
```
Note: When updating, you sometimes have to confirm with `y`.

### 6. Install and test the display

Please refer to the [display](/docs/guide/display.md) chapter on docs.
The only difference is that you can use the latest version of the Waveshare library when installing:
```
$ cd
$ git clone https://github.com/waveshare/e-Paper
$ cd ~/e-Paper/RaspberryPi*/python
$ sudo python3 setup.py install
```

### 7. Create and edit the config.ini

Start the app.py once.



The program is immediately aborted with "Exiting..." because the wrong display is still stored in the basic setting. But the config.ini was created in the background and you can open and edit it as described in chapter [edit config.ini](/docs/guide/edit_config.md).

### 8. Postprocessing

Everything else is as usual and listed in the [README](/README.md).

---

#### [option: lockout relay](/docs/guide/relay.md)  ᐊ  previous | next  ᐅ  [README](/README.md)

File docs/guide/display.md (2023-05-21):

## Set up and test the display

### Update display software

```
$ cd
$ git clone https://github.com/AxelHamburch/e-Paper/
$ cd ~/e-Paper/RaspberryPi*/python
$ sudo python3 setup.py install
```
`Info:` Normally cloning is done from the current Waveshare repository [https://github.com/waveshare/e-Paper](https://github.com/waveshare/e-Paper), but the new version currently still has problems with the recommended ATM configuration. Therefore, an older backup of "AxelHamburch" is recommended here for the time being.

###  Testing the display

`Note:` This is special for the "Waveshare 2in13 V2". Yours may be different, **check your version** carefully!

```
$ cd ~/e-Paper/RaspberryPi_JetsonNano/python/examples
$ sudo python3 ./epd_2in13_V2_test.py
```

If everything has been correctly connected and installed, the display will now show a demonstration and finally the screen will cleare.

`Help:`If it dosn't work, try the D-Version (flexible): `$ sudo python3 ./epd_2in13d_test.py`. Another option is the display "Waveshare 2in13 V3",  it is a new display. `$ sudo python3 ./epd_2in13_V3_test.py`. (Work is in progress to fully support the V3).
If you have a display from waveshare not listed here, try to find the right display type in the [waveshare repository](https://github.com/waveshare/e-Paper/tree/master/RaspberryPi_JetsonNano/python/examples).

display demo

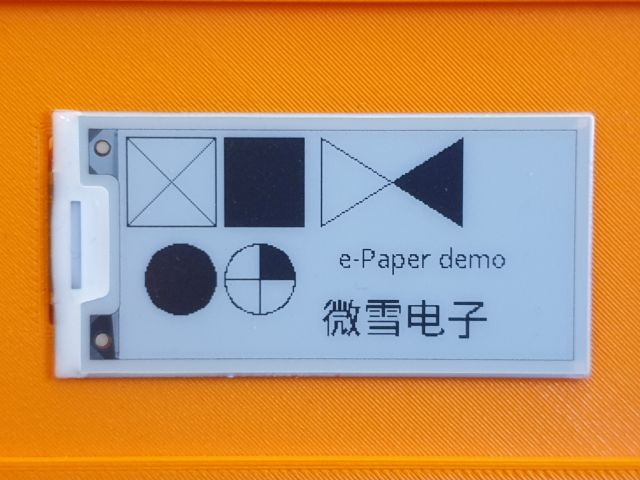
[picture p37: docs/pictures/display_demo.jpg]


display test example

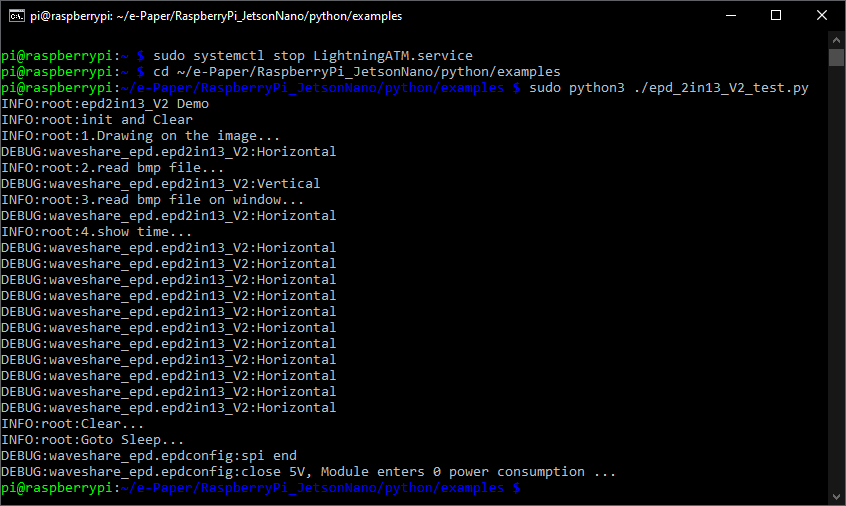
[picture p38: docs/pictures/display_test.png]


Possible source of error 

`AttributeError: 'SpiDev' object has no attribute 'writebytes2'`

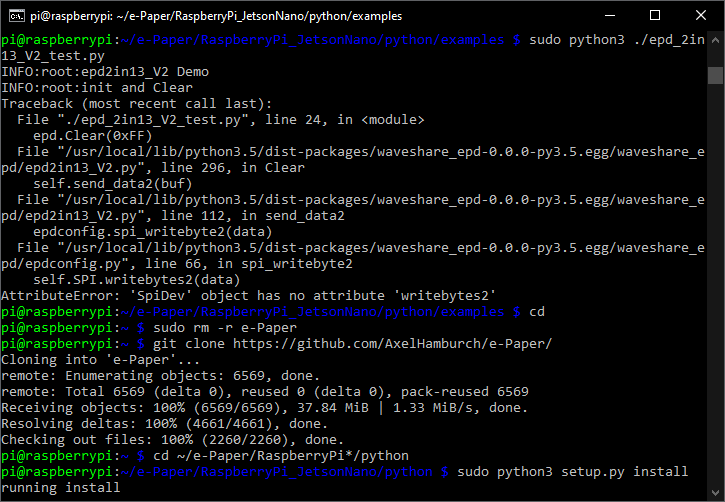
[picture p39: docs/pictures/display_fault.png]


Solution:

```
$ cd
$ sudo rm -r e-Paper
$ git clone https://github.com/AxelHamburch/e-Paper/
$ cd ~/e-Paper/RaspberryPi*/python
$ sudo python3 setup.py install
$ cd ~/e-Paper/RaspberryPi_JetsonNano/python/examples
$ sudo python3 ./epd_2in13d_test.py   # Change it to your version
```

`Note:` If it dose not work, check the wiring and your display version again.

---

#### [sdcard_and_wifi](/docs/guide/sdcard_and_wifi.md)  ᐊ  previous | next  ᐅ  [edit_config](/docs/guide/edit_config.md)

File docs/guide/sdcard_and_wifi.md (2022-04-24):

## Create SD card and write WiFi data to it

### Download the image and write it to the SD card

- Download the Raspbian image "2019-04-08-raspbian-stretch-lightningatm.gz" from the LightningATM Docs page
- [https://docs.lightningatm.me/lightningatm-setup/hardware-setup/assembly-and-software](https://docs.lightningatm.me/lightningatm-setup/hardware-setup/assembly-and-software)
- Write SD card image with Balena Etcher
- [https://www.balena.io/etcher/](https://www.balena.io/etcher/)
- Take out the SD card and put it aside

### Set up WiFi for the Raspberry Pi

Create a file named `wpa_supplicant.conf` with the following content:

```
ctrl_interface=DIR=/var/run/wpa_supplicant GROUP=netdev
update_config=1
country=DE

network={
	ssid="Home"
	scan_ssid=1
	psk="XXXXXXXXXXXX"
	id_str="Home"
}

network={
	ssid="Mobil"
	scan_ssid=1
	psk="12345678"
	id_str="Mobil"
}
```

- Change country code to your [area code](https://www.arubanetworks.com/techdocs/InstantWenger_Mobile/Advanced/Content/Instant%20User%20Guide%20-%20volumes/Country_Codes_List.htm)
- The file contains two WiFi networks. "Home" for home use and the "Mobil" for mobility
- "Mobil" can be you hotspot on your cell phone 
- Adjust the values for SSID and PSK as you like
- More networks can be added if needed
- Make sure the file ends with `.conf` and *not* with `.conf.txt`
- In the basic setting, Windows has the habit of hiding known file type extensions
- See "Folder Options/View/Advanced Settings"
- -> "Hide extensions for known file types" must be deselected!
- Slide the newly written SD card back into the slot of you computer
- -> The BOOT directory of the SD card is displayed
- Copy the new file `wpa_supplicant.conf` into it
- Insert the SD card into Raspberry Pi
- Note: After starting the Raspberry Pi for the first time, the ".conf" file disappears from the directory
- It can then be edited later via CLI by the command:
- `$ sudo nano /etc/wpa_supplicant/wpa_supplicant.conf` (the ssh connection is required, see next topic)

## Carry out basic software settings and updates

- Check the wiring again and then apply voltage
- Wait for a while and then look for the assigned WiFi IP in your own WiFi router
- Login to Raspberry Pi via CLI: `ssh pi@192.168.x.x`
- Confirm `The authenticity..` with `yes`
- Enter `raspberry` in the password prompt
- If you are logged in correctly you will now see: `pi@raspberrypi:~ $`

#### Adjust password and please remember!

```
	$ passwd
```

- Note: `$` stands for `pi@raspberrypi:~ $` in CLI and does not need to be typed

#### Perform an update, clone the ATM Github and install necessary additional options

```
	$ sudo apt update && sudo apt upgrade
	$ git clone https://github.com/21isenough/LightningATM.git
	$ cd LightningATM
	$ pip3 install -r requirements.txt
```

- Note: When updating, you sometimes have to confirm with `y` or `q`
- If everything was installed, disconnect the power supply and log in again via SSH and the the new password

---

#### [wiring](/docs/guide/wiring.md)  ᐊ  previous | next  ᐅ  [display](/docs/guide/display.md)

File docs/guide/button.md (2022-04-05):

##  Installation and test of the LED button

The most sensible option for the LightningATM is probably the button. An LED button is a nice feature but not essential, a simple button will do. 
With a button you can trigger the confirmation for the withdrawal process manually and is not dependent on a time control after inserting a coin. 
That makes it a little more relaxed. You can also use the button to access additional options.

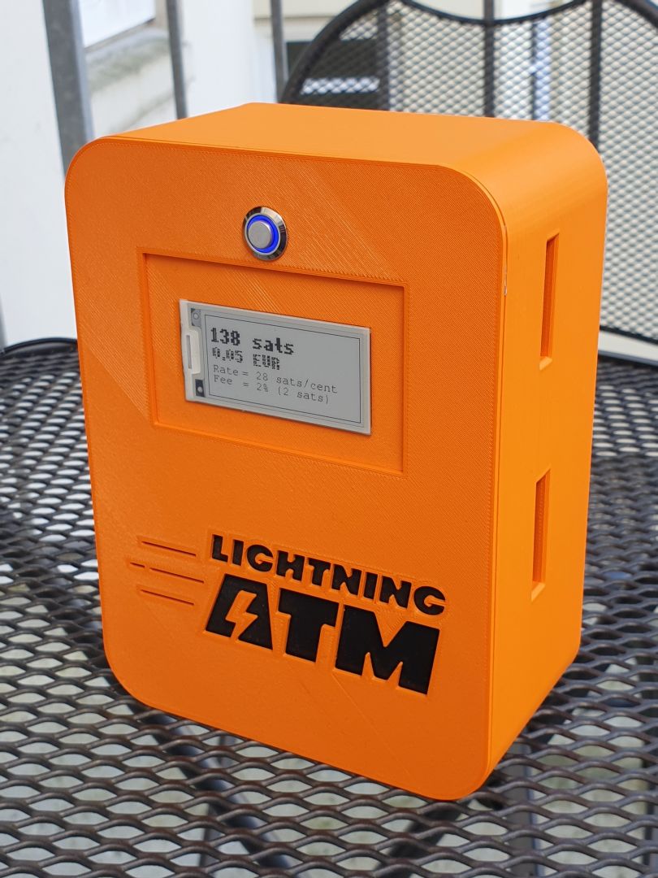
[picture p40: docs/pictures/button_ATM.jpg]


When the start screen is displayed, the button has four functions depending on the number of button presses:

1 : Shows screen: "No coins added! Please add coins first"  
3 : Simulates adding a coin (2 coin pulses, only for testing)  
5 : Show all possible display messages once 
7 : Shutdown the host machine  
9 : Reset Wallet (!!!) an scan new wallet credentials with camera  

If coins have been inserted, the LED goes on and the button only has the function of starting the withdrawal process and generating the QR code or activating the camera for scanning.

`Attention:` Nine pulses reset the wallet. If you don't have a camera to scan a new one, you'll have to set up a new wallet manually!

---

### Installation
  
The button is relatively easy to wire. See [wiring](/docs/guide/wiring.md). A soldering iron may be required. The individual poles must be measured unless this is clearly stated in the documentation for the button. The button closes the contact and is therefore NO (normal open) switching.

The LED is preferably designed for 3V. Slightly different voltages (e.g. 5V) can still work. Classic doorbell buttons often meet this requirement.
It is important that you **not** connect the LED directly between LED+ and GND! The output current would overwhelm the Raspberry Pi and possibly destroy it. Therefore, a resistor must always be connected in series to limit the current. It's a bit dependent on the LED used, but 220 or 330 ohms is a guide. Of course without warranty and guarantee! DYOR

Here is an [example](https://www.amazon.de/dp/B00UFNI47I/) for a small LED button that also fits well in the pocket version.

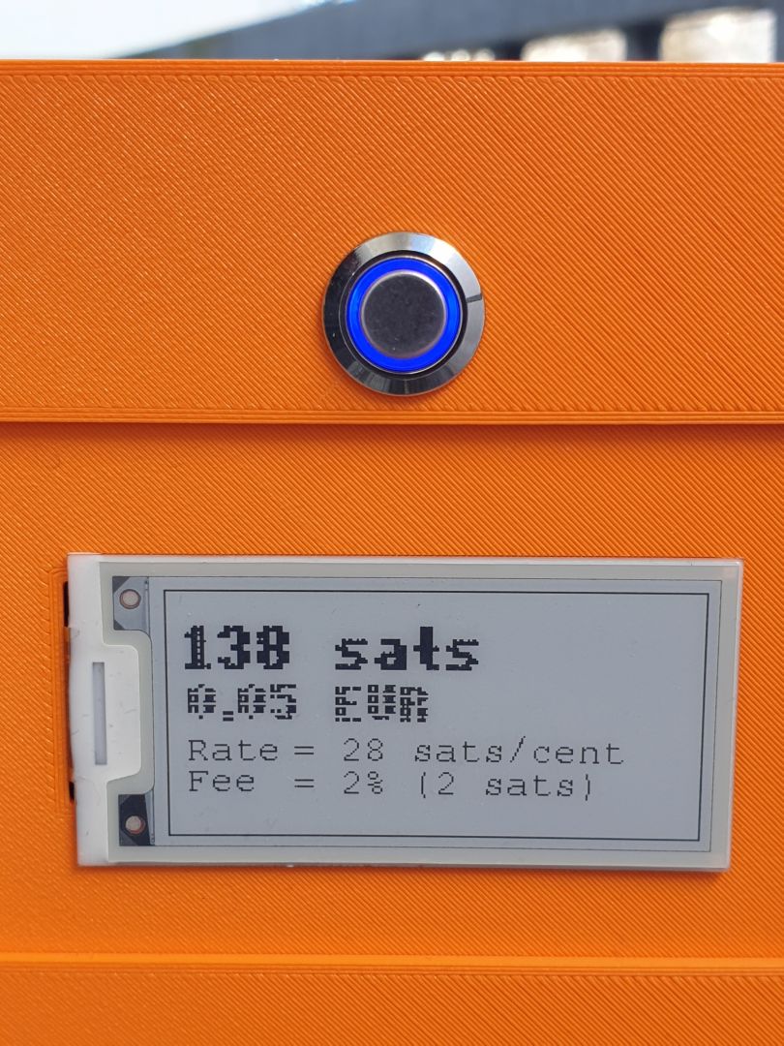
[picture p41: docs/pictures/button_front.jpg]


Here is the back. Protects cable routing for less movement at solder joints and mark the cable color. 

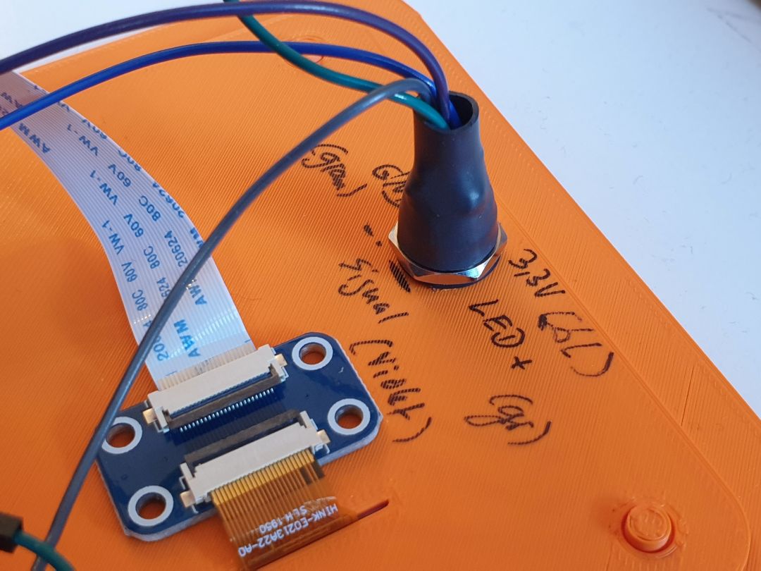
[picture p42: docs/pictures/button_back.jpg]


### Testing

It is best to test the button and the LED once after the installation. We have prepared small programs for this purpose. Log in to the ATM via CLI as usual. To be on the safe side, terminate the ATM service so that there are no overlaps.

	$ sudo systemctl stop LightningATM.service

Change to the following directory

	$ cd ~/LightningATM/tests

#### Start the button test program

    $ sudo python3 button_test.py
    
Here you can see the two button pushes as "event".

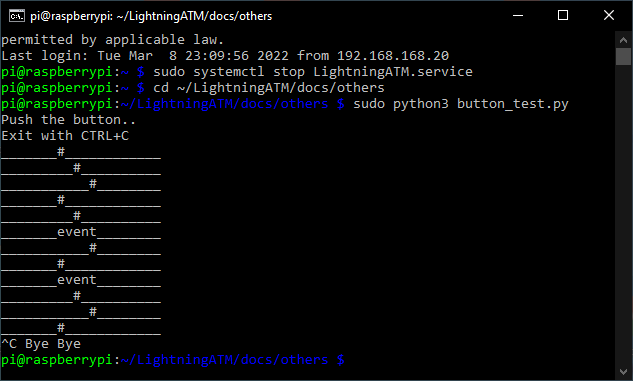
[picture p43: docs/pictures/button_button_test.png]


####   Start the LED test program

    $ sudo python3 LED_test.py
    
The LED program shows only that it is working and the LED should now flash.

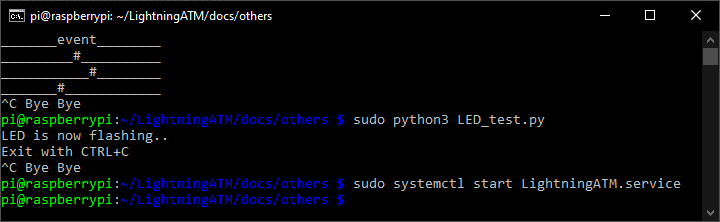
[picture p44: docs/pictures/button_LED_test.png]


#### Do not forget

 Restart the ATM service

    $ sudo systemctl start LightningATM.service

---

#### [option: language](/docs/guide/languages.md)  ᐊ  previous | next  ᐅ  [option: camera](/docs/guide/camera.md)

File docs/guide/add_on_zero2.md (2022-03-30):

##  Raspberry Pi image from scratch. (For example for the RPi Zero 2) 

#### `Warning:` It is not recommended to use the RPi Zero 2 for the Lightning ATM. However, if you already have one, you can use this guide to get it working. 

The Raspberry Pi Zero 2 is not supported in the Raspberry "Stretch" version. The tried and tested "2019-04-08-raspbian-stretch-lightningatm.gz" image does not run on the Zero 2. Accordingly, a new image must be created that supports the Zero 2. The current [Bullseye](https://en.wikipedia.org/wiki/Raspberry_Pi_OS) version (32-bit) does this. This image can be used for this, but still needs to be modified so that it can be used for the Lightning ATM.

Unfortunately, the new version does not support all components directly. The Waveshare displays are direct compatible and for the PaPiRus displays you have to install the library. 
  
This guide to creating a compatible version is only a guide. Deviations are possible and maybe even necessary. For the best result, however, it is recommended to stick to the procedure. Otherwise, troubleshooting support will be difficult. Since this is an experimental setting, any guarantee or warranty is excluded.
  
### The individual steps:

1. Creation of the raw image
2. Write the raw image with SSH and Wifi data
3. First start and first settings
4. Option: Install PaPiRus display library 
5. Carry out updates and installations
6. Install and test the display
7. Create and edit the config.ini
8. Postprocessing

---

### 1. Creation of the raw image

Find the appropriate Raspberry Pi OS (32-bit) image from the raspberrypi.org [Archive](https://downloads.raspberrypi.org/raspios_armhf/images/) and download it. You can use a newer version, but the "2022-01-28-raspios-bullseye-armhf.zip" version was tested for this tutorial. Unpack the file and write the image with [balenaEtcher](https://www.balena.io/etcher/). When done, remove the microSD.

### 2. Write the raw image with SSH and Wifi data

- Create an empty file named "SSH" in preparation. Make sure that the file has __no__ file extension such as ".txt". It is just called SSH and will later activate the SSH connection on the Raspberry Pi.
- Create a "wpa_supplicant.conf" file as described in chapter [sd card and wifi](/docs/guide/sdcard_and_wifi.md). This gives the Raspberry Pi the necessary information about your Wifi.
- Put the newly written microSD back into the computer slot and copy both files into the "boot" directory.
- Remove the microSD. It is now ready for the Raspberry Pi Zero.

### 3. First start and first settings

After starting the Zero 2 and waiting a few minutes. Then you can log in as described in the [sd card and wifi](/docs/guide/sdcard_and_wifi.md) chapter.

- Change the password and remember it!

		$ passwd
		
-   Activate the SPI interface for the display.

		$ sudo raspi-config






- Exit with "Finish".

### 4. Option: Install PaPiRus display library 

If you use a PaPiRus Display, you have to install the PaPiRus display library. If you have a Waveshare or other, you can cancel this step.

	$ curl -sSL https://pisupp.ly/papiruscode | sudo bash

Set it to Python 3



Choose your display size



### 5. Carry out updates and installations

It's the same like described in chapter [sdcard_and_wifi](/docs/guide/sdcard_and_wifi.md). Run the following commands one by one.

```
	$ sudo apt update && sudo apt upgrade
	$ git clone https://github.com/21isenough/LightningATM.git
	$ cd ~/LightningATM/
	$ pip3 install -r requirements.txt
```
Note: When updating, you sometimes have to confirm with `y`.

### 6. Install and test the display

As described in the [display](/docs/guide/display.md) chapter.

### 7. Create and edit the config.ini

Start the app.py once.



The program is immediately aborted with "Exiting..." because the wrong display is still stored in the basic setting. But the config.ini was created in the background and you can open and edit it as described in chapter [edit config.ini](/docs/guide/edit_config.md).

### 8. Postprocessing

Everything else is as usual and listed in the [README](/README.md).

Look at:

- [edit app.py](/docs/guide/edit_app.md)
- [tmux monitoring](/docs/guide/tmux_monitoring.md)
- [autostart](/docs/guide/autostart.md)

---

#### [option: lockout relay](/docs/guide/relay.md)  ᐊ  previous | next  ᐅ  [README](/README.md)

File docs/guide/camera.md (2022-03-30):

##  Installation and testing the camera

The camera is an optional feature and allows you to scan LNURL addresses. The 5MP Camera OV5647 is available from different manufacturers and with slightly different designs.
To test the function of the camera you can take a picture and download it to you computer.

### Installation

The ribbon cable is a bit special as the connectors on the camera and the Raspberry Pi are slightly different sizes. So the cable tapers.
Before sliding the cable into the slot, the black latch must be released by gently pulling upwards.
The cable can then simply be pushed in. The silver contacts must point away from the detent. See image!
When the cable is centered, you can lock the latches in place by sliding them back slightly.  

connection

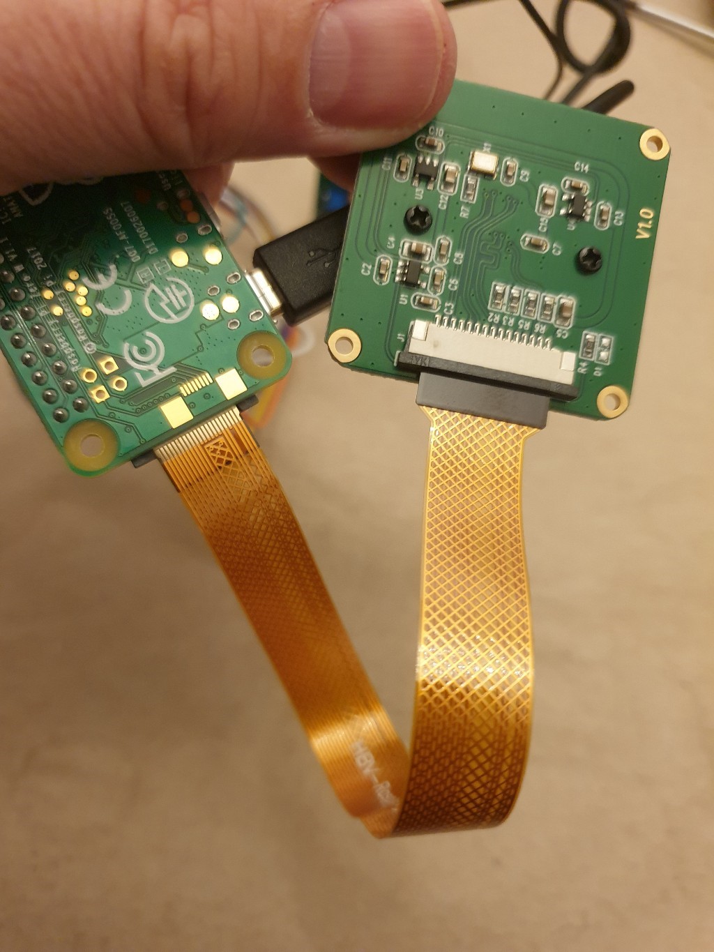
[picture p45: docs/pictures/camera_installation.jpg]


### Activate camera

- Login to the Raspberry Pi

      $ ssh admin@192.168.x.x
      
- Directory displayed: `pi@raspberrypi:~ $`
    
- Call up the Raspi-Config and activate the camera

      $ sudo raspi-config
    
- Choose: `Interfacing Options  Configure connections to peripherals` 
- Choose: `Camera      Enable/Disable connection to the Raspberry Pi Camera`
- Confirm: `Would you like the camera interface to be enabled?` -> `\<YES>` 
- Confirm: `The camera interface is enabled` -> `\<OK>`
- Go To: `\<Finish>`
- When ask for: `Would you like to reboot now?` -> `\<YES>`
- If you have not already restarted from the menu, then restart manually to activate the changes

      $ sudo reboot
      
raspi-config
  
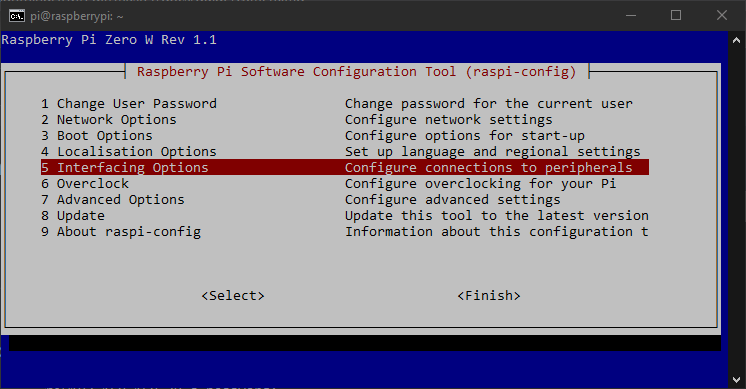
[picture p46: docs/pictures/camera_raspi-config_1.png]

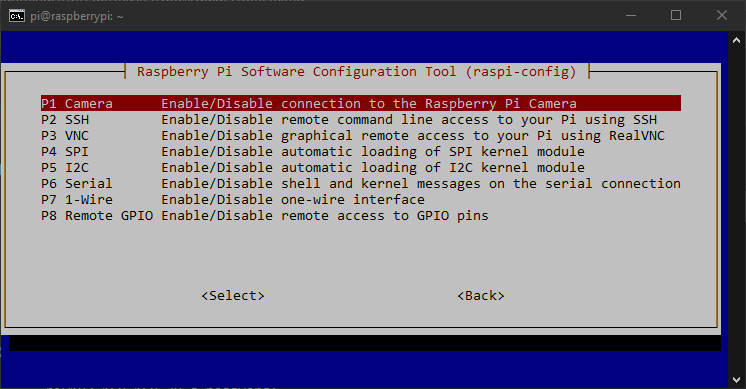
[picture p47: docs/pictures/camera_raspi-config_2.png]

  
  Your config menu can look slightly different, depends of you hard- and software
      
### Take a picture

- Take a picture after logging in to the Raspberry Pi

      $ raspistill -v -o test.jpg

  Note: The -v is only optional and will show more display data. The -o is necessary to write the file.
    
The recording lasts 5 seconds (time delay 5000 (ms)). You can shorten the recording time, but you should not make the time too short, otherwise the picture quality will suffer. One second (= 1000 ms) is definitely possible. The command then looks like:
    
   $ raspistill -v -o test.jpg -t 1000
   
  Further functions for a recording can be found in the help `$ raspistill --help`
  
- Check if the image has been saved

      $ ls -l
      
  The file `test.jpg` should now appear in the list.
  
- Check the directory structure

      $ pwd
   
  The directory should read: `/home/pi/`
  
 raspistill command

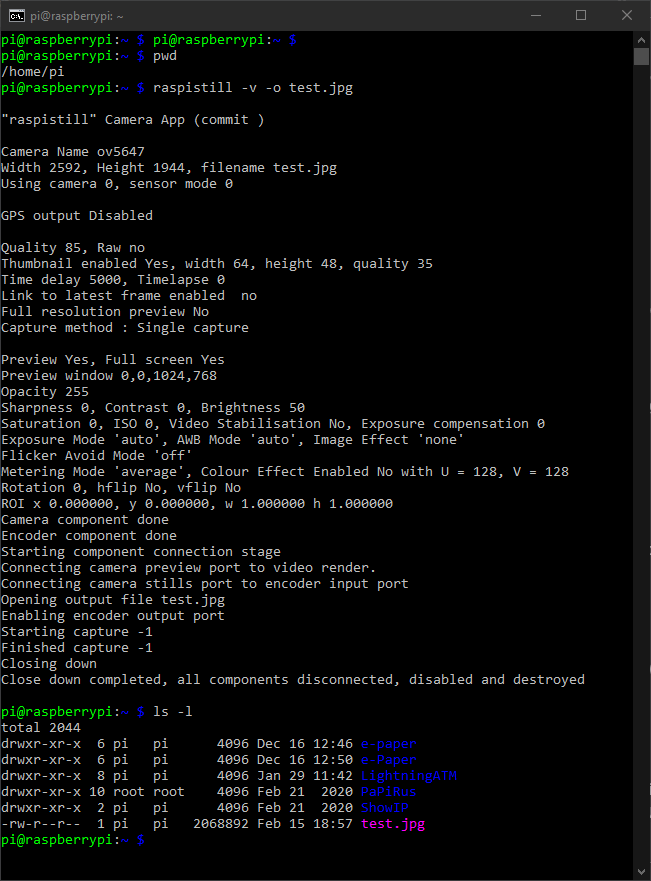
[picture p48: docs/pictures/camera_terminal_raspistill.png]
 
  
 ### Transfer the image to the computer
 
 - Open a *second terminal window* on the computer
 - Switch to a folder of your choice (example `C:\temp`)
 - The command to copy for a Windows system is

       $ scp pi@192.168.x.x:/home/pi/test.jpg .
      
   -> The password from the Raspberry Pi must be entered for comfirmation

 - If everything went well, the image was transferred to the computer and can now be vieweden
      
 - Note: The command is slightly different on a Mac or Linux system

       $ scp 'pi@192.168.x.x:/home/pi/test.jpg' ./
       
scp command

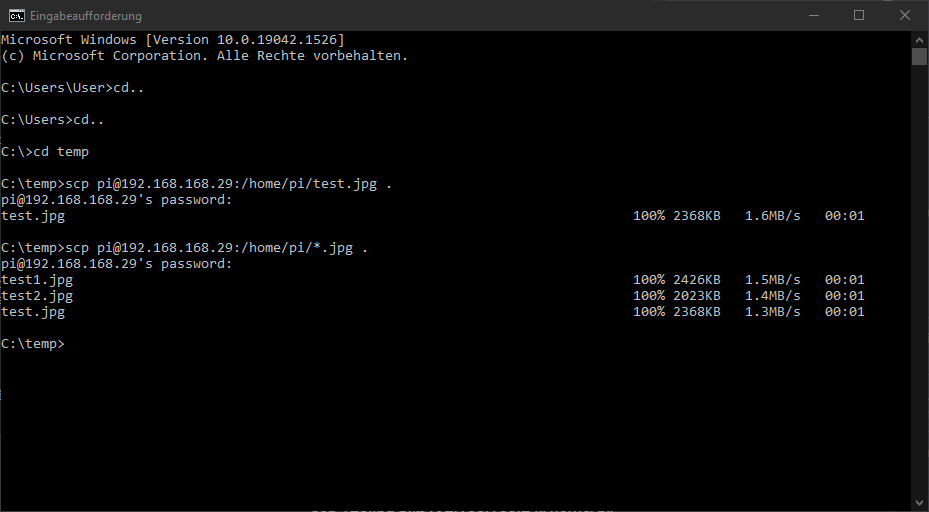
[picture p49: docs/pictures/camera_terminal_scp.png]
 
 
Example of a recording

The structure            |  The picture
:-------------------------:|:-------------------------:
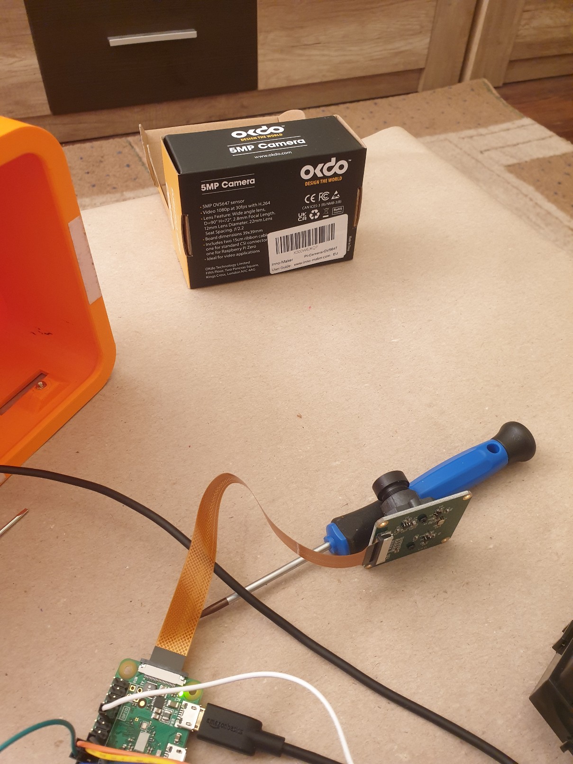
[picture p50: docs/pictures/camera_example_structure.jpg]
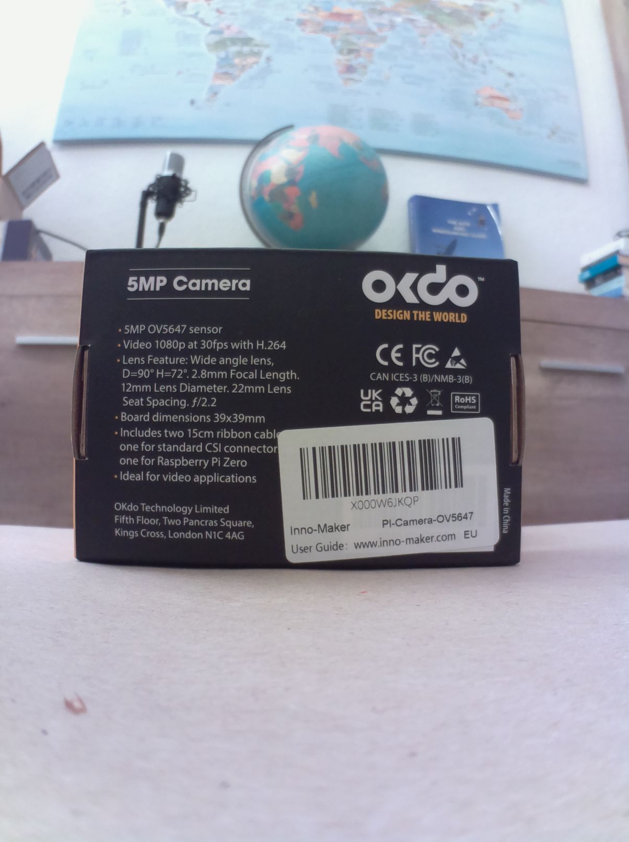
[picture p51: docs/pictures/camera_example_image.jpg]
  |  

Note: This camera was pretty cheap and has a variable lens that was pretty loose and difficult to adjust. You might want to use a better one for your project.
      
### Aditional hints

- If you want to take several pictures, the pictures must be numbered consecutively. E.g. test1.jpg, test2.jpg etc.
- Then you can transfer all images at once

      $ scp pi@192.168.x.x:/home/pi/*.jpg .   or    scp 'pi@192.168.x.x:/home/pi/*.jpg' ./
      
- You can do also videos. The command is `raspivid`

---

#### [option: button](/docs/guide/button.md)  ᐊ  previous | next  ᐅ  [option: lockout relay](/docs/guide/relay.md)

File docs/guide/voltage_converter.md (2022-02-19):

### Prepare the voltage converter

- Cut the micro USB cable. Approx. 15 cm from the Micro USB connector
- Strip both sides and solder together in parallel (++ / --) if you have a soldering iron, otherwise it has to be like this
- Place both ends on the input of the voltage converter and screw tight
- Connect the USB plug to the power pack or USB power pack
- Set the voltmeter to the correct measuring range. At least 35V DC
- Connect a voltmeter on the output side of the converter
- Using a screwdriver, turn the small rotary potentiometer (see picture) several times (probably first to the left) until the voltage shows 12.1 volts
- `Caution:` The initial voltage can be very high. It can be about 35 volts. So do not connect directly to the coin validator!
- Prepare cables for the output side:
- Connect plus (12V) and GND (0V) from the voltage converter to the coin validator
- Join a second wire from GND of the voltage converter (output) to the terminal 25 of the Raspberry Pi
- Check you wiring with pictures and [wiring diagrams](wiring.md)

voltage converter poti

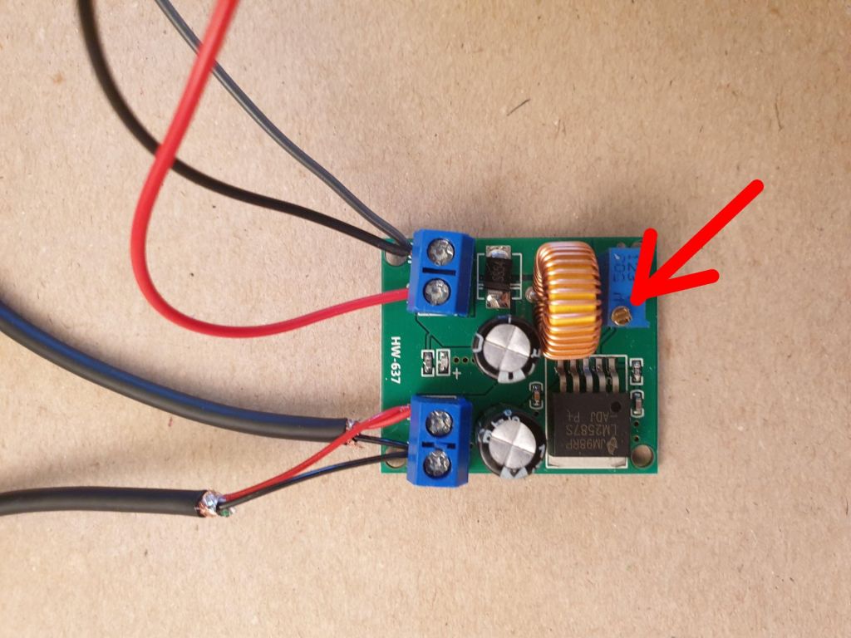
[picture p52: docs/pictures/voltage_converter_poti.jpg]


---

#### [README](/README.md)  ᐊ  previous | next  ᐅ  [coin_validator](/docs/guide/coin_validator.md)

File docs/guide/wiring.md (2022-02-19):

### Hardware wiring

- Wire the hardware according to the pictures, but do not yet install the ATM in the housing
- Set the switch on the e-Paper Display HAT to A and 0
- Be careful when plugging in the fine display ribbon cable!
- The clamp has a small lock and must be released beforehand. See pictures!

Wiring - Full Version
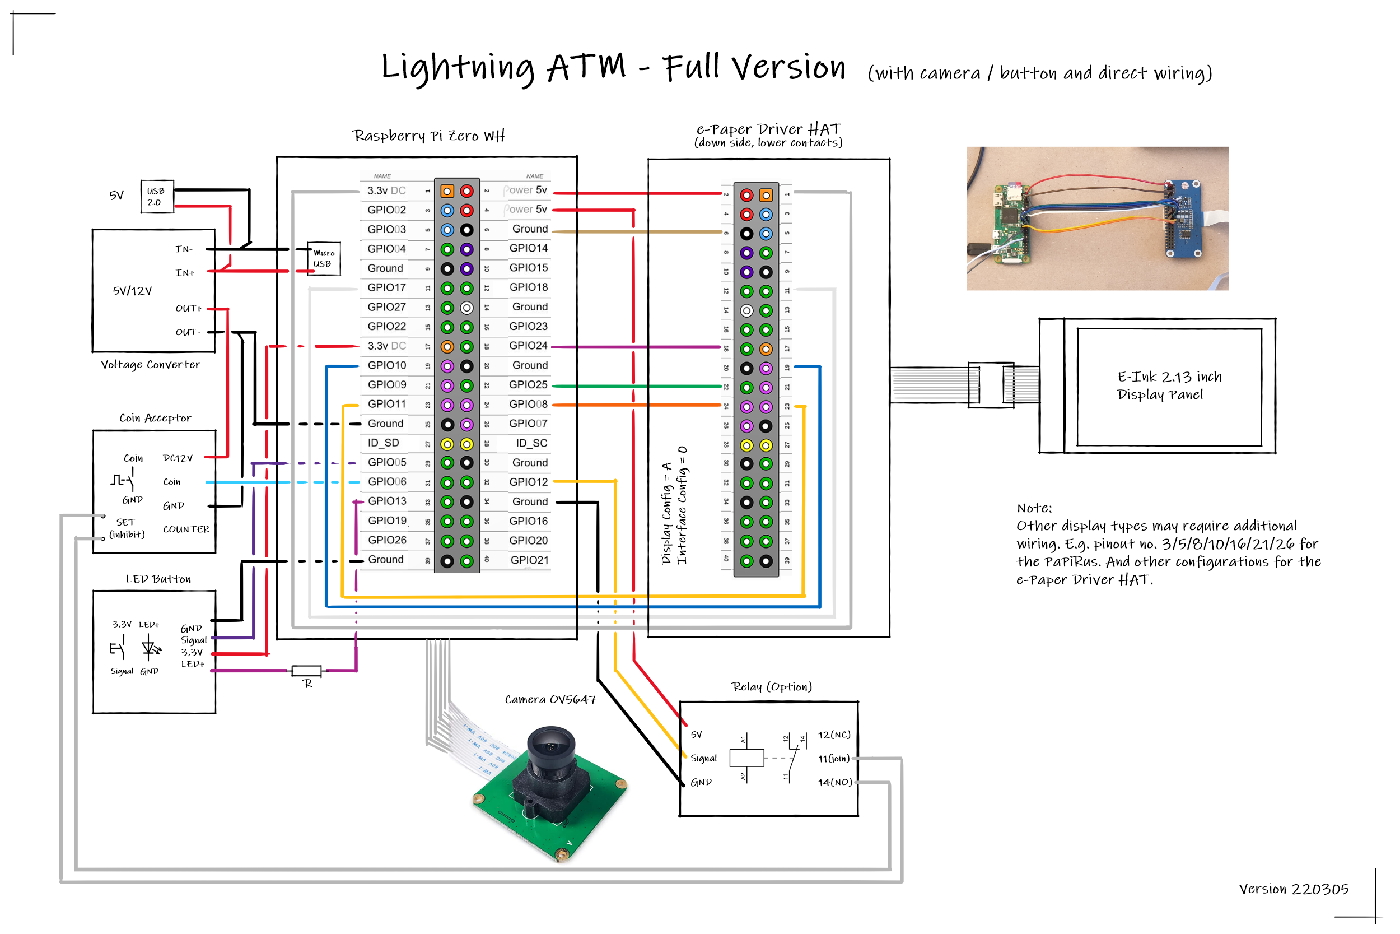
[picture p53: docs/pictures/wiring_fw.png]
Full Version


Wiring - Pocket Version
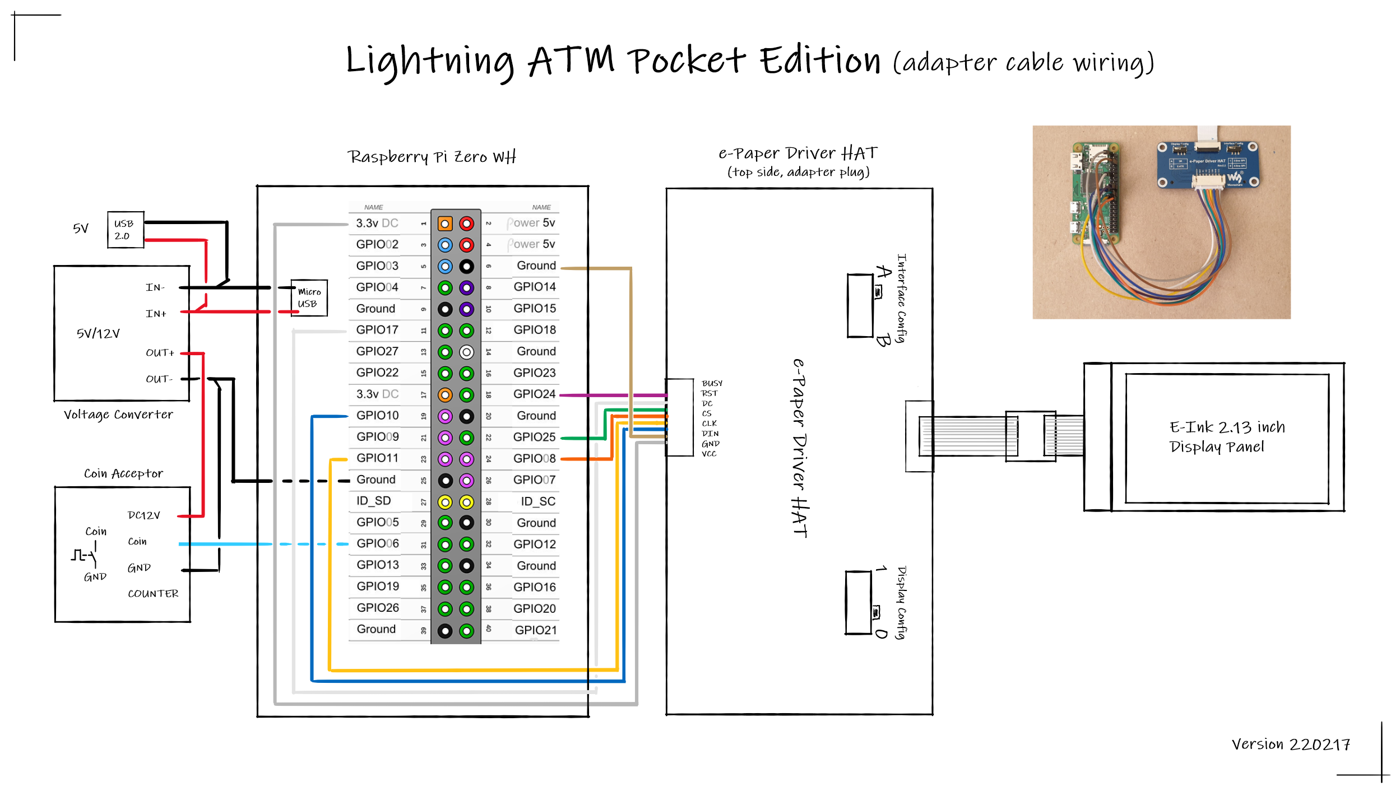
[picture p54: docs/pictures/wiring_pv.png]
Pocket Version


Clamp for ribbon cable

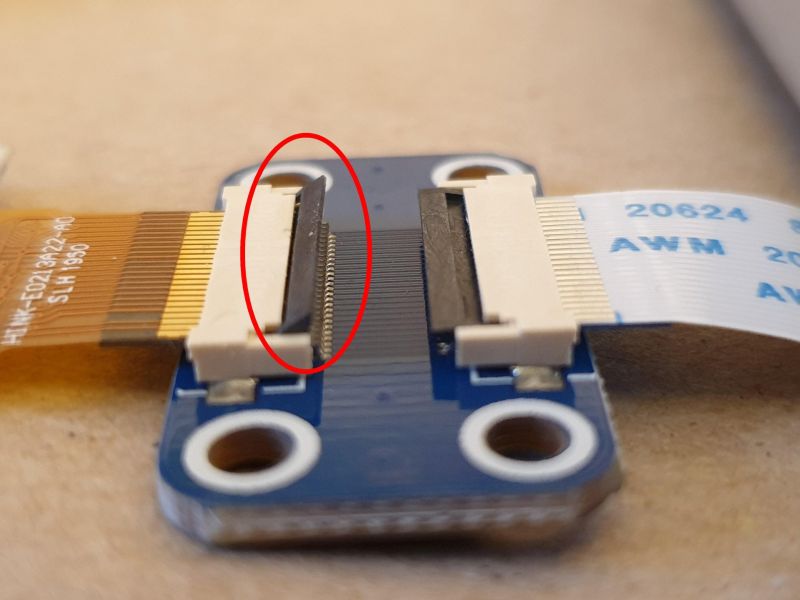
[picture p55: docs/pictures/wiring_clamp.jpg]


Pocket version adapter cable
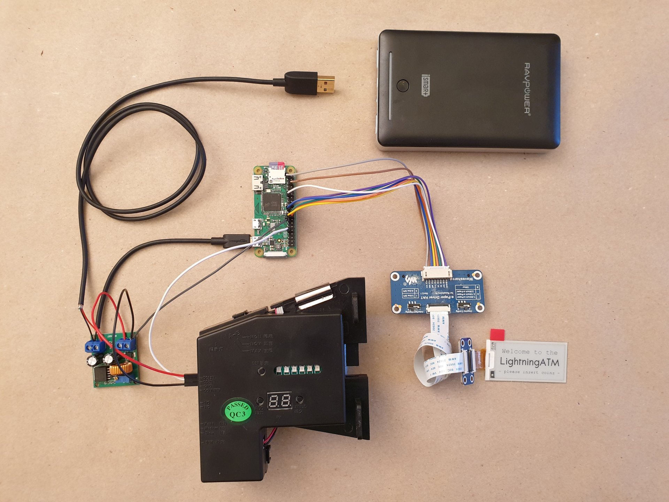
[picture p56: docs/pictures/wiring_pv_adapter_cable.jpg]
Pocket version adapter cable


Pocket version direct wiring
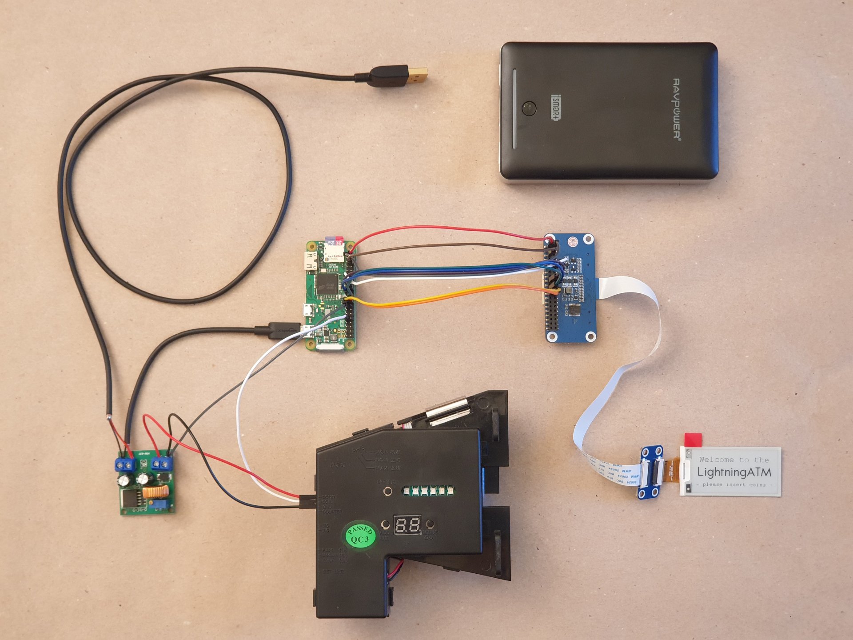
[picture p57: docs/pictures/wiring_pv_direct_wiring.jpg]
Pocket version direct wiring


Pocket version wiring build-in
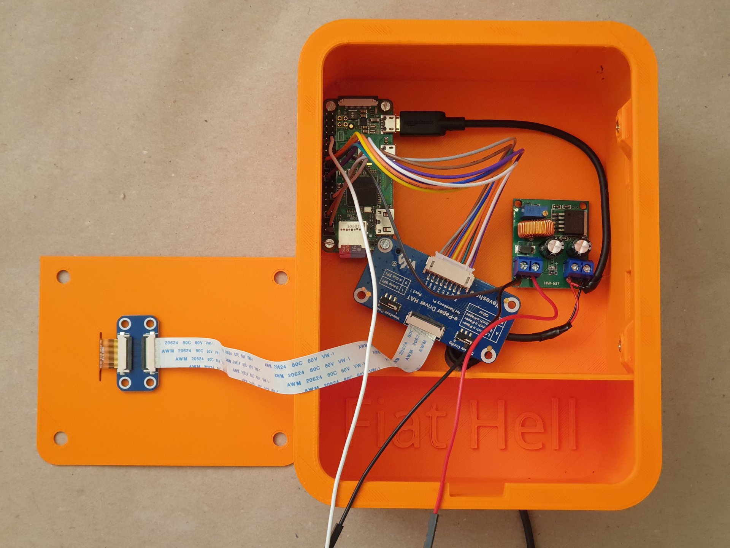
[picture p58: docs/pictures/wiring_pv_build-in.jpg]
Pocket version wiring bild in


Pocket version wiring build-in with coin validator             |  Direct wiring, without adapter cable
:-------------------------:|:-------------------------:
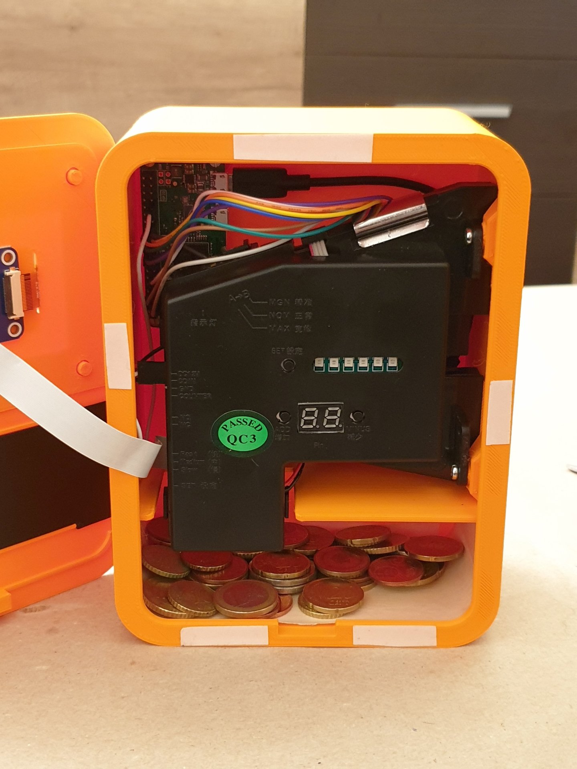
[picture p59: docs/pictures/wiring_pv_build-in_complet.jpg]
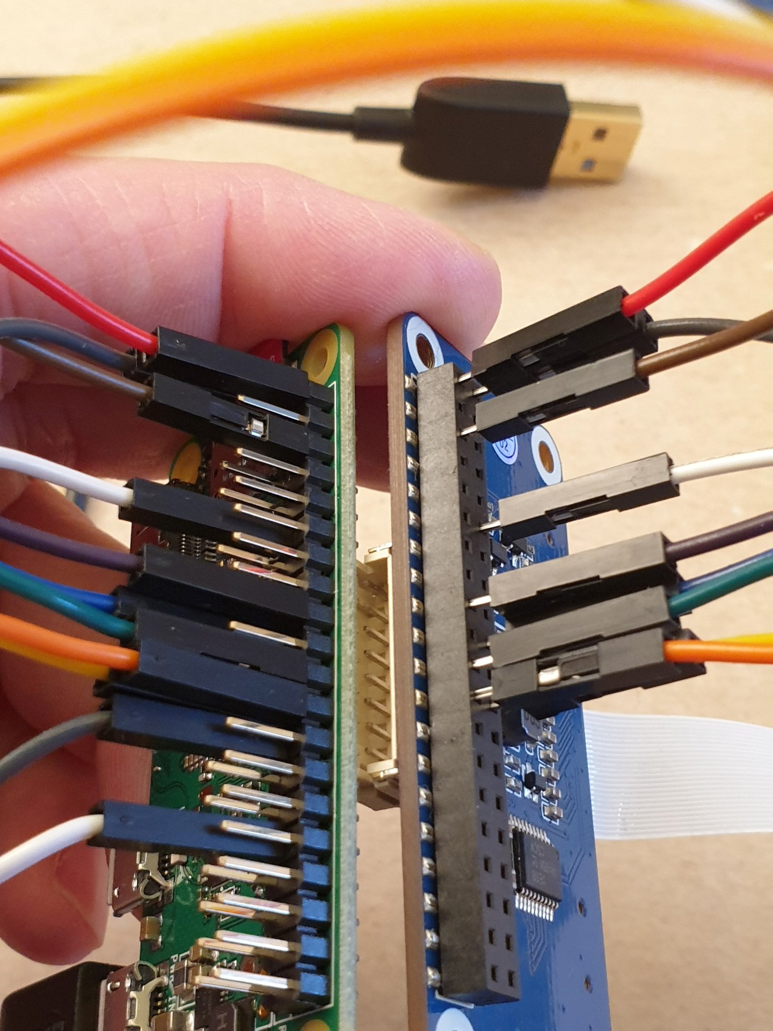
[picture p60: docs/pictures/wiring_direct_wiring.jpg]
  |  

---

#### [coin_validator](/docs/guide/coin_validator.md)  ᐊ  previous | next  ᐅ  [sdcard_and_wifi](/docs/guide/sdcard_and_wifi.md)

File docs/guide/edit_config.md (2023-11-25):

##  Setting the config.ini

Basic settings are made in `config.ini`. 

- Login on Raspberry Pi via CLI: `ssh pi@192.168.x.x`

### Start ATM once to create the config.ini

```
$ cd ~/LightningATM/
$ ./app.py
```

- When you first start you will get an "No display configuration matched. Exiting...".



- The config.ini has now been created in the background.
- Now edit the config.ini as described next step to set the display and other configurations.

`Note:` If the display is already set correctly, the process will not "Exiting..". You have to stop it with `CTRL+C`. 

### Open the config.ini file

```
$ nano ~/.lightningATM/config.ini
```

- Don't be surprised, the spelling is really `~/.lightningATM/config.ini` with a dot and lowercase letters.

### Set the config.ini file

#### Enter display type under `[atm]`

```
	display = waveshare2in13v2
```
`Note:` **Please compare your display type carefully!** Yours may require different settings and an incorrect setting will not work.

#### *Only for Pocket Version:* Delay time (set from 0 to 12 seconds)

```
	payoutdelay = 12 
```

- Its needed for the the pocket version, because it has no push button for confimrmation. The invoice will be generated automatically after 12 seconds.
- Note: If you have a button version, you must keep the 0.

#### Set activate wallet type / example LNbits 

- If you would like to set a BTCPayServer wallet, get further information here: [BTCPayServer](https://docs.lightningatm.me/lightningatm-setup/wallet-setup/lnd_btcpay) - NOT RECOMENDET -
- To use the Blink wallet as the funding source continue here: [Blink](/docs/guide/set_up_a_blink_wallet.md)
- Note: A quick guide how to set up an LNbits wallet find [here](/docs/guide/set_up_an_lnbits_wallet.md)

For LNbits:

```
	[atm]
	..
	activewallet = lnbits
```
```
	[lnurl]
	lnurlproxy = inactive
```

For Blink:

```
	[atm]
	..
	activewallet = blink
```
```
	[lnurl]
	lnurlproxy = active
```
Note: leave `lnurlproxyurl = https://api.lightningatm.me/v1/lnurl` like it is.

#### Under `[lnbits]` customize the data for the LNbits wallet

```
[lnbits]
# api credentials
url = https://legend.lnbits.com/api/v1
apikey = 
# One of "invoice" or "lnurlw"
method = lnurlw
# only for lnurlw - millisseconds to redeem the lnurlw
timeout = 90000
```
Note: Here you only need to specify the `apikey`. You get this from the [LNbits wallet](/docs/guide/set_up_an_lnbits_wallet.md), e.g. `apikey = 8682516eaf0c457...`

#### For Blink wallet customize the data unter `[blink]` 

```
[blink]
graphql_endpoint = https://api.blink.sv/graphql
api_key = blink_xxxxxxxxxxxxxxxxxxxxxxxxxxxxx
wallet_id = 5dxxxxxxxxxxxxxxxxxxxxx
```
Note: You can see how it works [here](/docs/guide/set_up_a_blink_wallet.md)

#### Next, set the coins to the pulses

- Each coin generates a specific number of pulses. Here 2 to 7 pulses.

```
[coins]
# Pulsecount, fiat value, name
coin_types = 2,0.05,5  eur cent
             3,0.10,10 eur cent
             4,0.20,20 eur cent
             5,0.50,50 eur cent
             6,1.00,1 eur
             7,2.00,2 eur
```

- When you finshed with changings in the config.ini, save and exit the editor: `CTRL+x -> y -> ENTER`
- `Note:` In the config.ini you can also change the currency and fees.

config.ini part 1 (example)
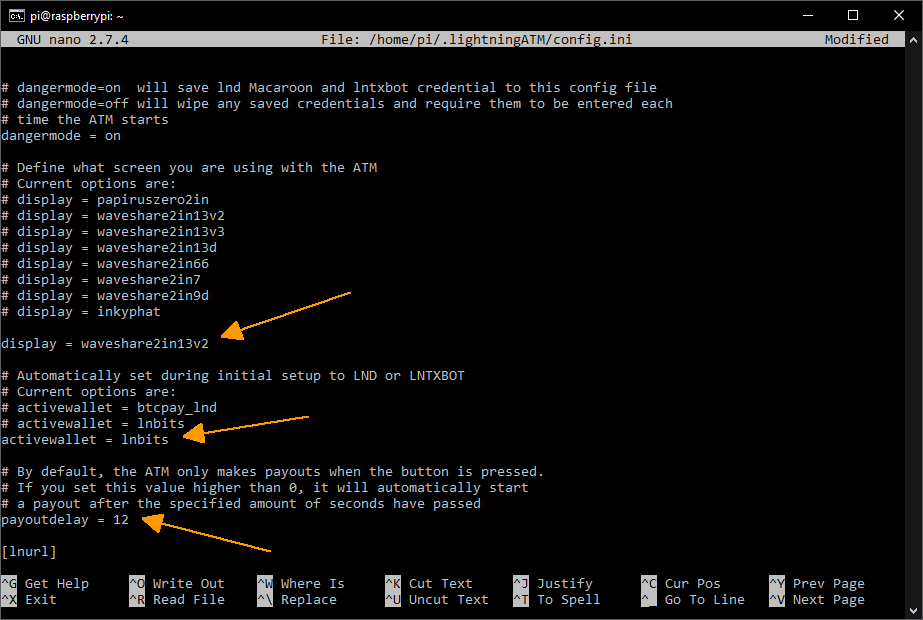
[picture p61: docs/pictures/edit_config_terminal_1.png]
config.ini part 1


config.ini part 2 (example)
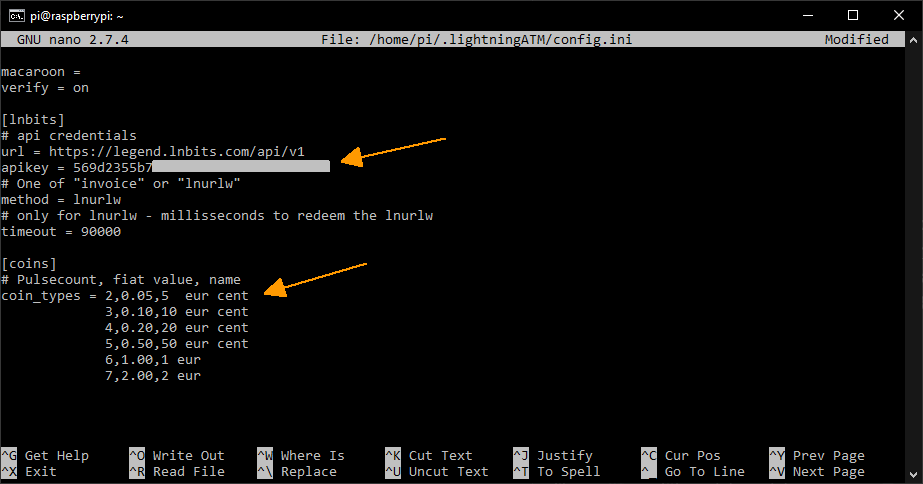
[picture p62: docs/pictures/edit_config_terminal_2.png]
config.ini part 2


#### Test the settings (or the entire ATM) once

- Start the ATM again

```
$ cd ~/LightningATM/
$ ./app.py
```

- The display should now show `LightningATM`
- If everything is entered correctly, the ATM should now be ready for use
- Just test it with few coins
- To stop the ATM just press `CTRL+C`
- After a short time, `Manually Interrupted` is displayed and you can see on the display that the `ATM is turned off`

display LightningATM

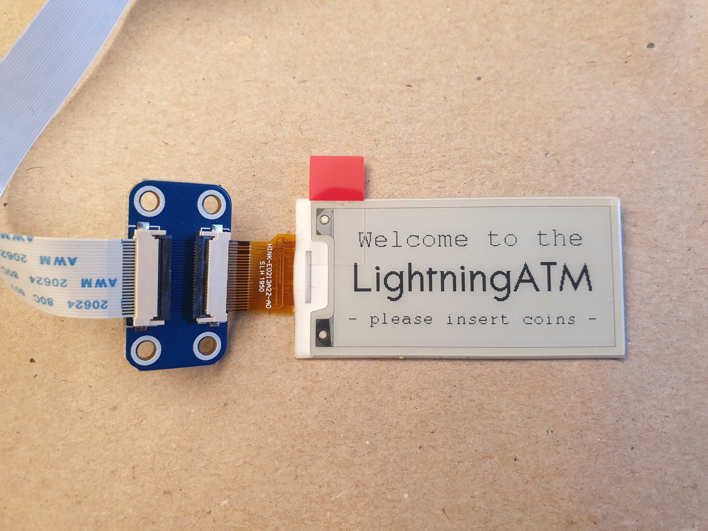
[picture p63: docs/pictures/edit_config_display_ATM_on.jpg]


display ATM turned off!

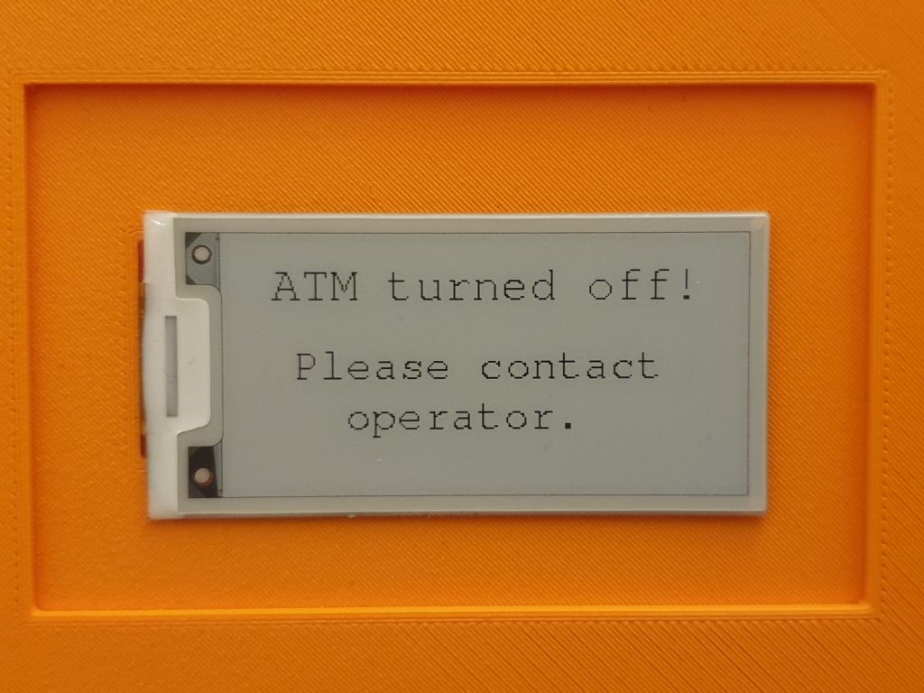
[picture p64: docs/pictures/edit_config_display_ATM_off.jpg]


- `Note:` If it doesn't work properly, you can run the debug logger with the command `tail -f ~/.lightningATM/debug.log` in a separate terminal window. We will show more information later in the chapter [`tmux`](/docs/guide/tmux_monitoring.md).
- `Note:` How to give the ATM an autostart function, you will learn later in chapter [`autostart`](/docs/guide/autostart.md)
- `Note:` If you have already set the autostart and also start the app.py manually as described here, the display will not work properly. Then first stop the service as described in [`autostart`](/docs/guide/autostart.md).

---

#### [display](/docs/guide/display.md)  ᐊ  previous | next  ᐅ  [debugging and tmux](/docs/guide/tmux_monitoring.md)

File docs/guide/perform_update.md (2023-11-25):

## Instruction to update the ATM 📜🧐

We have now added LNbits and Blink as a new funding source for the LightningATM. 🎉

### 1. Quick guide on how to set up an LNbits wallet or Blink wallet

A quick guide how to set up an LNbits wallet find [here](/docs/guide/set_up_an_lnbits_wallet.md)

A quick guide how to set up an Blink wallet find [here](/docs/guide/set_up_a_blink_wallet.md)

### 2. Update the LigthningATM 

Connect the ATM to the power supply and log in to your LightningATM via [Wifi/SSH](https://github.com/21isenough/LightningATM/blob/master/docs/guide/sdcard_and_wifi.md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). You may find the IP in the network of your router. Open a command line editor and write the command `ssh pi@192.168.x.x`. Hopefully you still have the assigned password. We will now load the new repository on the ATM and activate it. You have to stop the `LightningATM.service` once, otherwise you will get a strange display and the ATM will not work properly.  

    $ sudo systemctl stop LightningATM.service
    $ cd ~/LightningATM
    $ git pull
    
Now your ATM is set to the new version. Next you have to configure it for the new wallet.
    
### 3. Edit the config.ini

    $ nano ~/.lightningATM/config.ini

#### Add the following lines at the very end for LNbits and 🆕 for Blink

```
[lnbits]
# api credentials
url = https://legend.lnbits.com/api/v1
apikey = 
# One of "invoice" or "lnurlw"
method = lnurlw
# only for lnurlw - millisseconds to redeem the lnurlw
timeout = 90000

[blink]
graphql_endpoint = https://api.blink.sv/graphql
api_key = blink_xxxxxxxxxxxxxxxxxxxxxxxxxxxxx
wallet_id = 5dxxxxxxxxxxxxxxxxxxxxx
```

`Note for LNbits:` Customize your `apikey = 8682516eaf0c457...` from the LNbis wallet. See [here](/docs/guide/set_up_an_lnbits_wallet.md)

`Note for Blink:` Customize your `api_key` and `wallet_id` from Blink wallet. See [here](/docs/guide/set_up_a_blink_wallet.md). 

#### Change active wallet to LNbits

    [atm]
    ..
    activewallet = lnbits

#### Or change active wallet to Blink

    [atm]
    ..
    activewallet = blink

and

    [lnurl]
    lnurlproxy = active
    
#### In case you have a very old config.ini. Check this too.

    [atm]
    ..
    # Set language: "en", "de", "fr", "it", "es", "pt", "tr" currently available
    language = en

    # Do you have a camera? "False" or "True"
    camera = False
    
Example, see [here](https://github.com/21isenough/LightningATM/blob/master/example_config.ini).
    
Save and exit editor: `CTRL+x` -> `y` -> `Enter`
   
### 4. Start ATM for testing

    $ cd LightningATM
    $ ./app.py

- It takes a few seconds for the display to update..
- The ATM has started and you can use it normally or test the functions.
- Stop the ATM with `CTRL+C`

To debug: Launch a second terminal window, login with ssh and access logs with 

    $ tail -f ~/.lightningATM/debug.log
    
Log file to debug
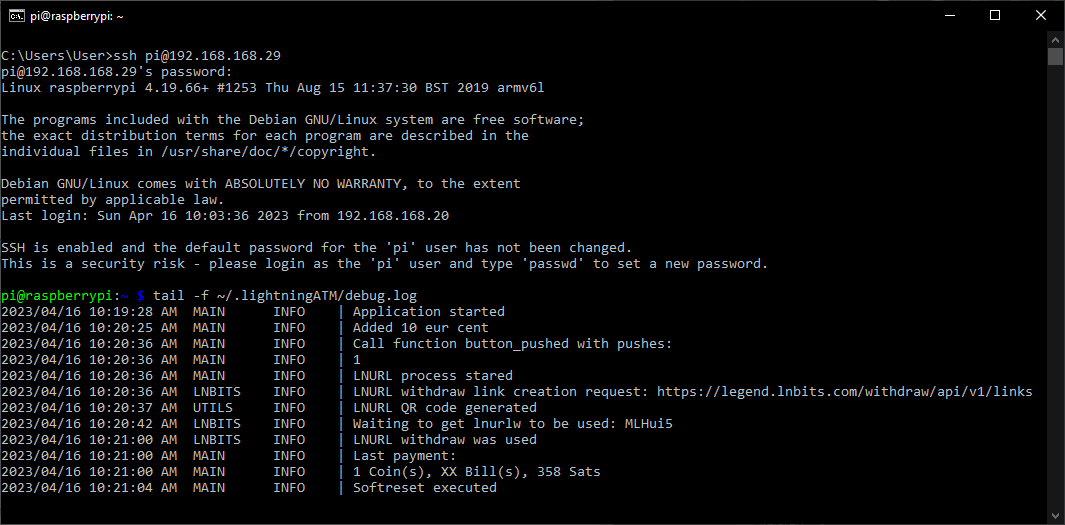
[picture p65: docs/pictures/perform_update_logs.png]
Log file to debug


### 5. Final step

Restart the LightningATM service by power cycle

    $ sudo systemctl start LightningATM.service

- Your ATM should now restart as usual

#### [README](/README.md)  ᐊ  previous

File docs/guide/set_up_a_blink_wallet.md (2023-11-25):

# How to set up a Blink wallet

This is a minimal guide to set up Blink (ex Bitcoin Beach Wallet) account as a funding source for the LightningATM.<br />
Get more info and download the app from [blink.sv](https://blink.sv). To learn more about the API visit [dev.blink.sv](https://dev.blink.sv) or discuss on the [Galoy Mattermost](https://chat.galoy.io).

## Get the credentials from the Blink Dashboard

* open the [Blink Dashboard](https://dashboard.blink.sv)
* log in with your email or phone number if you are using Blink already
* if you have no account yet can create a new one by logging in with a phone number

### Wallet ID
* once logged in to dashboard find the wallet IDs under the balances

  wallets

* copy the BTC wallet ID to pay out from the BTC balance
* copy the USD wallet ID to pay out from the Stablesats balance
* paste the wallet ID into the config.ini file under the `[blink]` section

### API key

* create a new key on the `API Keys` tab
* give it a name and choose a `Scope` which permits to send payments (Read and Write)
* the default expiry is 90 days

  api_key

* copy the key (starting with `blink_` ) and paste it into the config.ini file under the `[blink]` section

## Set the config.ini file

* in the `[atm]` section set the `activewallet` to `blink`

  ```
  activewallet = blink
  ```

* in the `[lnurl]` section set the `lnurlproxy` to `active`

  ```
  lnurlproxy = active
  ```

* the `[blink]` section must include these:

  ```
  [blink]
  graphql_endpoint = https://api.blink.sv/graphql
  wallet_id = 5dxxxxxxxxxxxxxxxxxxxxx
  api_key = blink_xxxxxxxxxxxxxxxxxxxxxxxxxxxxx
  ```

* A complete example of a `config.ini` using the pocket version of the ATM without a button with USD coins:
  ```
  [atm]
  cur = usd
  centname = cent
  language = "en"
  camera = False
  fee = 0
  dangermode = on
  display = waveshare2in13v2
  activewallet = blink
  payoutdelay = 10

  [lnurl]
  lnurlproxy = active
  lnurlproxyurl = https://api.lightningatm.me/v1/lnurl

  [btcpay]
  url =

  [lnd]
  macaroon =
  verify = on

  [lntxbot]
  url =
  creds =

  [lnbits]
  url = https://legend.lnbits.com/api/v1
  apikey =
  method = lnurlw
  timeout = 90

  [blink]
  graphql_endpoint = https://api.blink.sv/graphql
  api_key = blink_xxxxxxxxxxxxxxxxxxxxxxxxxxxxx
  wallet_id = 5dxxxxxxxxxxxxxxxxxxxxx

  [coins]
  coin_types = 2,0.01,1  usd cent
              3,0.05,5 usd cent
              4,0.10,10 usd cent
              5,0.25,25 usd cent
              6,1.00,1 usd
  ```

## Notes
* remember to top up the funding wallet with some sats
* easiest to monitor the payouts if you are logged in to the Blink app on your phone
* be aware when testing that paying the same account is not allowed (cannot withdraw from the LightningATM to the same account from which the credentials are used)
* note the date of the expiry of the API key (valid for 90 days by default) and create a new one before the ATM stops working

#### [edit_config.md](/docs/guide/edit_config.md)  ᐊ  previous

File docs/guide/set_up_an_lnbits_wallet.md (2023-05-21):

## Quick guide on how to set up an LNbits wallet

- Go e.g. to the [ledgend.lnbits.com](https://legend.lnbits.com/) demo server
- Assign a name and press `ADD A NEW WALLET`
- Bookmark the page and/or copy and paste the URL to a safe place. This will log you in to your wallet.
- Understand the warning! It is a demo server for testing. Keep only the necessary Satoshis in the wallet. 
- See a pop-up menu box on the right or bottom labeled `API info` and open it.
- You should see `Admin key: 8682516eaf0c457...`. The number-letter combination is the 'apikey' that you will need afterwards.
- But before that you need to install an extension. Go to `Extensions`, search for `LNURLw` and activate it with `ENABLE`.
- Fund the wallet with a few thousand Satoshis.

LNbits Wallet
LNbits Wallet

#### [edit_config](/docs/guide/edit_config.md)  ᐊ  previous

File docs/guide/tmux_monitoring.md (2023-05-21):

## Monitoring system "tmux" to control the processes

The easiest way to monitor multiple processes at the same time is to open multiple windows. So you can open one for the "app.py" and one for the debug logger `tail -f ~/.lightningATM/debug.log` and then display them side by side. But to watch both processes at the same time in one window, you can use "tmux" (terminal multiplexer). This allows the terminal window to be split vertically into two parts.

###### Install tmux

```
$ cd
$ sudo apt install tmux    
```

###### Necessary commands for the terminal multiplexer (tmux) 

```
CTRL + b -> % = split window
CTRL + b -> right or left arrow = change the window
CTRL + b -> CTRL + right or left arrow = move dividing line
CTRL + b -> d = back to single window
```

###### Start and use tmux

```
$ tmux
```

- Split tmux windows: `CTRL+b -> %`
- Switch between left and right window: `CTRL + b -> right or left arrow`
- If necessary, move the dividing line: `CTRL+b -> CTRL + arrow right or left`

###### Start the `app.py` process (ATM) in the left window

```
	$ cd ~/LightningATM
	$ ./app.py
```

- `Note:`  If you have already activated the autostart function, problems can arise if you start the app.py in the tmux window at the same time. Therefore, it is better to end the service `sudo systemctl stop LightningATM.service` for the tmux and activate it again later `sudo systemctl start LightningATM.service`. See next chapter [`autostart`](/docs/guide/autostart.md).

######  Start `debug.log`

- Switch to the right window and paste or type

```
	$ tail -f ~/.lightningATM/debug.log
```

- Back to single window: `CTRL+b -> d`

Example tmux window

tmux window

Two withdrawals were made here. Once 5 cents and once 10 cent. Left side you see the pulses. Right side you see the coins to it. 2 pulses = 5 Cent = 199 Sats and 3 pulses = 10 Cent = 399 Sats. After that the program was stopped manually with CTRL+c.

---

#### [edit_config](/docs/guide/edit_config.md)  ᐊ  previous | next  ᐅ  [autostart](/docs/guide/autostart.md)

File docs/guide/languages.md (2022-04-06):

## How to set a another language

The ATM offers the option of setting a different language via `config.ini`. That's relatively easy. But in order to make the whole thing look nice, we still have to manually adjust a few texts for our display.

---

### 1. Set language in config.ini

To do this, you have to log in to the ATM via SSH `$ ssh pi@your-ip` and your password and then open the config.ini.

      $ nano ~/.lightningATM/config.ini

The config.ini:



Here you can select one of the languages. E.g. "language = de" for German. When you're done, save and exit the editor with `CTRL+x -> y -> ENTER`.

Now restart the ATM with the new language setting

    $ sudo systemctl restart LightningATM

### 2. The fine adjustments

You will probably not be entirely happy with the way the display looks. This is because the texts in the different languages are of different lengths. The English language is also usually very short, which means that the translations often extend beyond the display and cut off words. Since the ATM supports different display types and we don't know many languages will come, we can't set and fix all possibilities. So you have to set this up for your set yourself.

#### 2.1 View all pages one by one

If you have a button on your ATM, it's easy now. Simply press the button 5 times and all possible displays will be shown briefly once.

If you don't have one, you have to start a small program. To do this, log in again and enter the following commands one after the other.

    $ cd ~/LightningATM/
    $ python3 ./tests/displayalign.py

-> The ATM will now show all possible displays and finally restart itself, if the autostart is still acitve.

Now that you've seen all the display pages, you've probably noticed one or the other page where you might want to change the text position or the text size or maybe even the text itself. It's best to go through the whole thing again and take pictures of the displays you might want to change. You will then use these to identify the texts and make settings. 

#### 2.2 Change the text

That's the easiest. Just go to the text message file an edit it.

    $ nano ~/LightningATM/displays/messages_de.py

- If you want to change another language, just change the "messages_de.py" into "messages_es.py" for Spanish for example.
- Info: The english version is called "messages.py".
- After you are satisfied, save the changes and close the editor with `CTRL+x -> y -> ENTER`. Then test the whole thing again as described in point 2.1 or restart the ATM with `$ sudo systemctl restart LightningATM` to update and then press the button to see the messages again.
- `One request:` If you think your translation works well and you want to help us, please copy and paste the entire text into a plain text file like "messages_xx.txt" and DM it to AxelHamburch from the Telegram Group. 🙏

Example: messages_de.py



#### 2.3 Alligne the text

Now comes a slightly difficult part. You can adjust the font size and text position for each display. To do this, you first need to know which display type you have and secondly what the text block (function) is called that you want to edit. You can get the display type from "config.ini" and it is in between "display = ". For example: "waveshare2in13v2". The best way to get the name for the text block is from the text display messages. See point 2.2. This can be e.g. `# Text for update_startup_screen()`. The text block is therefore called `update_startup_screen()`.

Now you going to edit the Python file for the display and look for the text block (function).

     $ nano ~/LightningATM/displays/waveshare2in13v2.py

- `Note:` Swap the "waveshare2in13v2.py" to your display type you use. E.g. "waveshare2in13d.py" for the D version.

Here is an example for the "update_shut_down" text block (function):



The before and after pictures:

before           |  after
:-------------------------:|:-------------------------:
  |  

The alignment for the above before / after pictures:



If you set everthing you think it will help, exit the editior with `CTRL+x -> y -> ENTER` and restart the ATM `$ sudo systemctl restart LightningATM` or got to point 2.1 and start the test program again to see the result. 

### Annotation

I hope this could help you and you are happy with the result. 💛

`Note:` We recommend backing up your changes somewhere. Just copy the text or parts of it and save it somewhere convenient. If you update once the ATM, your changes are gone. So you can easily restore your settings again.

`Note:` If you have problems and don't know where they come from, you can [update](/docs/guide/we_need_your_help.md) the ATM. Then everything except the config.ini is overwritten and is new. Everything should be fine again and you also have the latest version.

---

#### [information_and_tips](/docs/guide/information_and_tips.md)  ᐊ  previous | next  ᐅ  [option: button](/docs/guide/button.md)

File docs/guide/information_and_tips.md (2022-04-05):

## Aditional information and tips

- You can get more help in the Telegram group: [https://t.me/lightningatm_building](https://t.me/lightningatm_building)
- When making entries in the terminal window (CLI = Command Line Interface), it is best to copy and paste the commands: 

  > Copy the command to the clipboard with `STRG+C` and then point to the blinking cursor in the CLI window and press the right mouse button to paste the clipboard into the terminal window. (If it doesn't work, make the terminal window "activ" - with one left click on the window or even move the curser with tap space bar - befor you do the right click.)
- If you get the error `bash: $: command not found`, you may have copied the dollar sign "$" in front of the command. Don't do that!
- When logging in via SSH, make sure to use the correct user `pi`. If you accidentally use `admin` or make a typo, you will not see an error, but the password will not be accepted
- You can change WiFi parameters with the command: `$ sudo nano /etc/wpa_supplicant/wpa_supplicant.conf`
- A collection of the most used commands for quick access:

  ```
  cd ~/LightningATM/
  ./app.py
  nano ~/.lightningATM/config.ini
  tail -f ~/.lightningATM/debug.log
  sudo systemctl status LightningATM.service
  sudo systemctl stop LightningATM.service
  sudo systemctl start LightningATM.service
  ```
---

#### [autostart](/docs/guide/autostart.md)  ᐊ  previous | next  ᐅ  [option: language](/docs/guide/languages.md)

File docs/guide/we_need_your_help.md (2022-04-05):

## Stagnation is regression. Update your ATM! 📜🧐

Many updates have been made in the last two months. 💪😅 Updates for more reliability and some nice features. See the [guidelines](https://github.com/21isenough/LightningATM#installation-guideline) for more information and try it out.

--- 
## Steps to update
### 1. Expand the config.ini with "language" and "camera" (If not allready done)

Because we are also expanding the config.ini with this update, we unfortunately have to expand config.ini manually, otherwise we get an error message when starting the ATM. Expanding is not difficult and does not have to be undone later. First we logon again via SSH and stop the LightningATM service and call up the config.ini.

    $ sudo systemctl stop LightningATM.service
    $ nano ~/.lightningATM/config.ini
    
Then we add the following text between `centname = cent` and `# Set the Fee in %`

    # Set language: "en", "de", "fr", "it", "es", "pt", "tr" currently available 
    # Code 2 from https://www.science.co.il/language/Codes.php
    language = en

    # Do you have a camera? "False" or "True"
    camera = False
    


- When you finshed with changings in the config.ini, save and exit the editor: `CTRL+x -> y -> ENTER`
- `Help:` If you want to copy and paste the text, take the text to the clipboard and then place the cursor where you want to paste the text and right-click to paste. But important is just `language = en` and `camera = False`.

### 2. Update to the new version

Logon via SSH and stop the LightningATM service, make a backup from directory LightningATM, clone the new Github to "temp", sync once from "temp" to "LightningAMT" and then delete the "temp" directory that is no longer needed.

    $ sudo systemctl stop LightningATM.service
    $ cp -r -v LightningATM LightningATM_Backup
    $ git clone --branch master https://github.com/21isenough/LightningATM.git temp
    $ rsync -a temp/ LightningATM/
    $ sudo rm -r temp
   
### 3. Start and test the version

    $ cd LightningATM
    $ ./app.py

- It takes a few seconds for the display to update, but then..
- The ATM has started and you can use it normally or test the functions.
- Stop the ATM with `CTRL+C`
- If something went wrong or you just want to watch the ATM, launch a second terminal window, login via ssh and call the debugger: `$ tail -f ~/.lightningATM/debug.log`
- If you like this version? Just keep it and delete the Backup: `$ cd` and then `$ sudo rm -r LightningATM_Backup`

### 4. If you don't like this version and want to get rid of it 

Make the backup the major version again and then delete the backup.

    $ cd
    $ rsync -a LightningATM_Backup/ LightningATM/
    $ sudo rm -r LightningATM_Backup

- Everthing should now be as befor. Even the wallat data.
- You can clean up the coinfig.ini, but you don't have to.

### 5. Final step

Restart the LightningATM service

    $ sudo systemctl start LightningATM.service

- Your ATM should now restart as usual
- If you find some issues or have some suggestions call @AxelHamburch in the telegram group or on Github

## Thank you for your support! ❤️

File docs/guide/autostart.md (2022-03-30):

## Autostart and start/stop the ATM

######  Install and activate the autostart service:

```
$ cd ~/LightningATM
$ sudo cp LightningATM.service /etc/systemd/system/LightningATM.service
$ sudo systemctl enable LightningATM.service
$ sudo reboot
```

- From now on the ATM will start automatically after booting.

######  Commands to control the ATM:

```
$ sudo systemctl status LightningATM.service
$ sudo systemctl stop LightningATM.service
$ sudo systemctl start LightningATM.service
```

- `Note:` When the autostart service is once installed and activated, you only need to "start" the ATM if you previously stopped the ATM.
- `Note:` If you want to observe the app.py in tmux, you musst `stop` the "LightningATM.service" manually, bevor you start the app.py in the tmux. Then restart the ATM with the "start" command or simply restart the entire ATM afterwards by unplugging the power and plugging it back in.

---

#### [debugging and tmux](/docs/guide/tmux_monitoring.md)  ᐊ  previous | next  ᐅ  [information_and_tips](/docs/guide/information_and_tips.md)

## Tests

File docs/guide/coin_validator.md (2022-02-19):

### Configure the coin validator (set 6 coins / e.g. 5 cents to 2 euros)

- Set the switches on the coin validator to "NO" (contact normal open) and "Medium" (medium pulse speed).
- Apply the 12V to the coin validator (without Raspberry Pi) => The coin validator will flash and show 0 (zero)
- Press and hold simultaneously the ADD and MINUS buttons until A appears in the display
- When B appears, switch back to A by ADD or MINUS
- Press SET (slowly), then E will appear on the display
- This indicates: You are in them menu to set the amount of differnet coin types 
- Set it to 6 (6 coins = 5 cents to 2 euros) with ADD (or MINUS) and press SET
- Now the display shows H1 (for the first coin). The first of 6 LEDs has come on
- Now specify how often the coin should be inserted for calibration
- Set to 20 with ADD (or MINUS) and then press SET
- The display now shows P1 for further settings of coin 1 and you can define the output signal
- 5 cents = 2 pulses / 10 cents = 3 / 20 cents = 4 / 50 cents = 5 / 10 euros = 6 / 2 euros = 7
- Set to 2 pulses (for 5 cents) with ADD (or MINUS) and then press SET
- The last thing on the display is F1, which represents the accuracy of the coin recognition. The value 8 worked well
- Set to 8 with ADD (or MINUS) and then press SET
- The parameters for the first coin have now been set 
- Now the second LED is on and the display shows H2
- Now repeat the same steps again for the second coin (e.g. 10 Cent) up to coin 6 vor (e.g. 2 Euro)
- When all coins are set, all LEDs flash briefly to confirm and the display shows A again
- After a short time, 0 (zero) appears again in the display

### Calibrating the coin validator

- Press the SET button (slowly) twice
- The first LED light and A1 will show in the display
- Now insert the first coin (5 cents) 20 times
- Use as many different coins as posible
- Finally all LEDs flash to confirm and the display shows A2
- Repeat for the remaining coin types
- All LEDs flash briefly again to confirm and the display shows 0 (zero) again
- The coin validator is now ready

coin validator

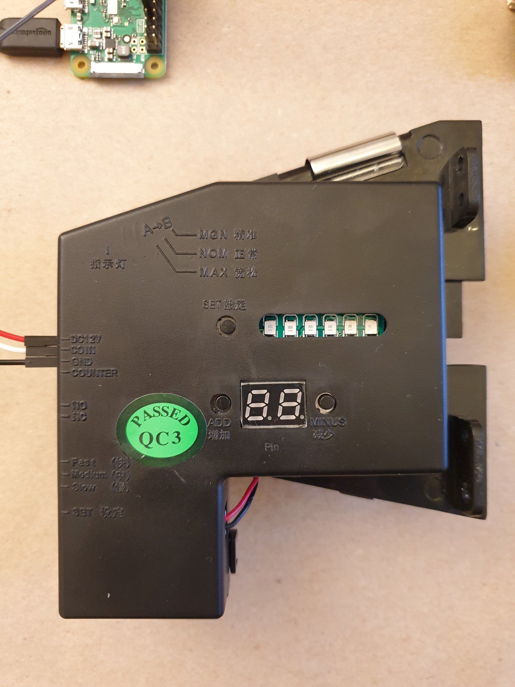
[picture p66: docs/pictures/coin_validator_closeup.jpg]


coin calibration
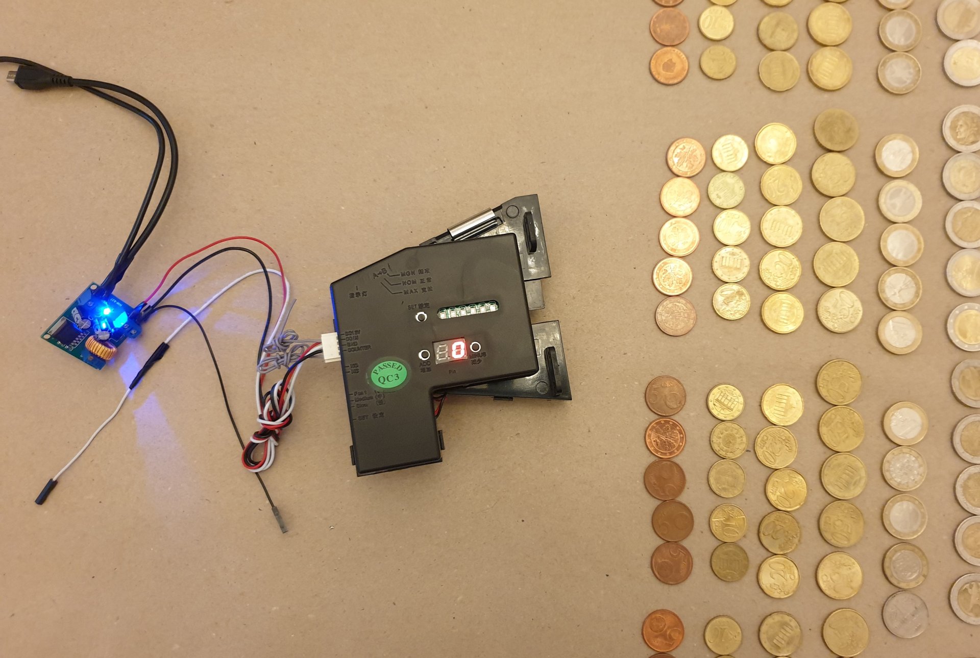
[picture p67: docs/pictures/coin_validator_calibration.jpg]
coin calibration


---

#### [voltage_converter](/docs/guide/voltage_converter.md)  ᐊ  previous | next  ᐅ  [wiring](/docs/guide/wiring.md)

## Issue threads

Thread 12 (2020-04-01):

Add support for additional screens (E-Ink, TFT, LCD)

21isenough, 2020-04-01:
**Actual Behavior:**
Currently the LightningATM works only with one screen - PaPiRus Zero - ePaper / eInk Screen (display.py). It is hard to procure and expensive.

**Expected Behavior:**
The ATM shall work with a variety of different screens. Not only E-Ink but also TFT and LCD screens.
- https://www.waveshare.com/product/mini-pc/raspberry-pi/displays/e-paper/2.7inch-e-paper-hat.htm?___SID=U

talentpierre, 2020-04-03:
interested. i programmed a untested halfway prototype for LCD, TFT, TouchScreen

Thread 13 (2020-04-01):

Remove the dependency "pycoingecko"

21isenough, 2020-04-01:
**Actual Behavior:**
Currently the ATM relies on the python library "pycoingecko" for the exchange rate. It's a (quick and dirty) replacement for the recently closed API of bitcoinaverage.com

**Expected Behavior:**
Since this is only one simple GET request to the CoinGecko API, this could simply be done in python and does not need a library. Remove and use the "requests" package in python.

https://github.com/21isenough/LightningATM/blob/8f81224948e17a36a00d65396a0204c84316f767/utils.py#L53

Closed 2020-04-06.

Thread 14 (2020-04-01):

Add smarter way of detecting and counting the inserted coins

21isenough, 2020-04-01:
**Actual Behavior:**
Each of 6 different coins sends a certain amount of pulses to the RaspberryPi, that are then registered on a GPIO pin.

A variable is set to the amount of pulses and regularly read to determine the inserted coin. This leads to slight delays and coins can't be inserted too fast after one another.

**Expected Behavior:**
I imagine, it would be better to continuously populate an array with pulses (a representation thereof)   and evaluate this array in a thread. This should allow for faster "coin insertions" and make the user experience smoother.

pppest, 2020-05-09:
good idea. I would say this also depends on the coin slot hardware so one would have to test the pulse time. but the pulses could be saved in a list with a time stamp and then later be read. dont think a thread is necessary but that might depend on what you use. i use kivy and it comes with a clock that allows for call back functions. Ill take a look.

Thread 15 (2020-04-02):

Add admin menu to configure the ATM

21isenough, 2020-04-02:
**Actual Behavior:**
Currently we can only access different functions on the ATM with "multiple button presses" (e.g. button 3 times pressed, starts the Lntxbot scanning process).

**Expected Behavior:**
There shall be an "Admin Menu" that can be controlled with only one button. It could be a menu with all the menu points and an arrow next to the first point.
- One press on the button makes the arrow jump to the next menu point
- Two presses on the button confirm that menu point, and executes the function.

pppest, 2020-05-09:
even better.  maybe use some of the gpios w jumpers? so that when power on the raspi automatically know the setting?

danielcharrua, 2023-05-10:
Any thoughts of adding a web UI menu? Like connecting to the IP of the ATM and tweak some options from a web UI? Maybe that would be nicer to use the unique button to move or confirmation...

Let me know your thoughts.

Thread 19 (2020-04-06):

Check if performance gain can be achieved with different price querying

21isenough, 2020-04-06:
**Actual Behavior:**
Currently the bitcoin price is fetched once the first coin has been inserted.

**Expected Behavior:**
Might gain some response time if the price is fetched in a regular interval rather than after the first coin.

kimasplund, 2020-06-13:
Would it not be better if price is fetched at first coin insert, but fetched again and locked in on send?

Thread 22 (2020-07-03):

solution for using waveshare 2.13inch_e-Paper_HAT

VitaminB21, 2020-07-03:
Is there a solution for using this display?

https://www.waveshare.com/wiki/2.13inch_e-Paper_HAT#Raspberry_Pi

21isenough, 2020-07-03:
Hey @Lace79

No yet. But I've ordered one of these displays and am exploring it right now. Will work soon since it's a cheaper and more broadly available display.

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

Lace79, 2020-07-03:
Thank you! OK great, i hope it works soon.
I tried it, but I'm still to noobie

21isenough, 2020-07-03:
We'll get there, yes. It's a great project to learn some more :+1:

Lace79, 2020-07-03:
You're right, learned a lot, but now i'm lost.

21isenough, 2020-07-03:
Yes, now with this new E-Ink we need to add another library and quite some code to make this work.

Lace79, 2020-07-03:
OK
I don't know if i can help, but if let me know

21isenough, 2020-07-07:
Working on this in a different branch here:
https://github.com/21isenough/LightningATM/tree/waveshare-screen

FutureTravelATM, 2020-08-27:
We added the WaveShare 2.7 inch screen which works on the same libary as the Waveshare 2.13. The 2.7 does not do a partial screen refresh, so refresh is about 6 seconds....

Attached is the pinout for the screen using the included 8pin screen connector.

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

lightisfaster, 2022-01-22:
done.

Closed 2022-01-22.

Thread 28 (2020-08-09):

Pressing the button with no coins inserted leads to generating a QR-code

Danstrg, 2020-08-09:
Just a little check needed if coins have been inserted before generating the Qr-code

AxelHamburch, 2022-03-11:
This problem is already fixed. If no coins are inserted and the button is pressed, the "display.update_nocoin_screen()" screen is called up. See app.py line 88.

danielcharrua, 2023-06-26:
@lightisfaster @AxelHamburch this issue is already solved, please close this.

AxelHamburch, 2023-07-01:
@lightisfaster you can close this

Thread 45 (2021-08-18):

Impulses of fast insertion of coins are accumulated

tkachuk-labs, 2021-08-18:
Seems like if I'm able to insert coins fast enough in sequence, impulses for coins are accumulating. For example let's say I do have 3 similar coins, which are mapped to impulse number 2 on coins acceptor. I do insert them very fast in sequence. Then ATM will detect 3 coins corresponding to impulses 2, 4 and 6.

lightisfaster, 2022-02-07:
Thanks for create this issue. Unfortunately we haven't found a solution for this yet. Maybe someone has an idea?

AxelHamburch, 2022-02-19:
I was able to reproduce the problem. I have a possible solution that requires a small relay, since the coin validator does not have a inhibit input. Whenever coins were inserted, I would deactivate the release coil for the passage of the coins, so that the coins that are thrown in immediately after being thrown in are ejected again. I need a place in the program where we can set an output that will switch a relay for a certain amount of time or until we can say for sure it's safe to add the second coin now. But I'm still at the beginning and the hardware ist just arrived. I will give an update as soon as I know more.

AxelHamburch, 2022-03-27:
This issue will be solved with the PR #64
https://github.com/21isenough/LightningATM/pull/64
See details here:
https://github.com/AxelHamburch/LightningATM/blob/update_gpio/docs/guide/relay.md

AxelHamburch, 2022-04-05:
It's no in the current version. Use the ralay an the the problem is solved.
@lightisfaster can we close this topic?

danielcharrua, 2023-06-26:
@lightisfaster @AxelHamburch I think this issue is solved and can be closed.

AxelHamburch, 2023-07-07:
@lightisfaster
Pls close

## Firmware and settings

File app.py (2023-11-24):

#!/usr/bin/python3

import logging
import os
import sys
import time
import math
import subprocess

from gpiozero import Button, LED

import config
import lndrest
import lntxbot
import qr
import lnbits
import blink

import utils
import importlib
from PIL import Image


# Initialize inputs and outputs
button_signal = Button(5, False)
coin_signal = Button(6)
button_led = LED(13)
lockout_relay = LED(12)

display_config = config.conf["atm"]["display"]
display = getattr(__import__("displays", fromlist=[display_config]), display_config)

logger = logging.getLogger("MAIN")


def check_connectivity(interface="wlan0"):
    output_lines=subprocess.check_output(["wpa_cli","-i",interface,"status"])
    for output_line in output_lines.decode("utf8").split("\n"):
        if output_line[0:4]=="ssid":
            # We have an SSID
            return output_line[5:]
    return None


def softreset():
    """Displays startup screen and deletes fiat amount
    """
    # Inform about coin, bill and sat amounts
    if config.COINCOUNT > 0:
        logger.info("Last payment:")
        logger.info("%s Coin(s), XX Bill(s), %s Sats", config.COINCOUNT, config.SATS)

    config.SATS = 0
    config.FIAT = 0
    config.COINCOUNT = 0
    config.PUSHES = 0
    # Turn off button LED
    button_led.off()
    
    display.update_startup_screen()
    logger.info("Softreset executed")


def button_event():
    """Registers a button push event
    """
    config.LASTPUSHES = time.time()
    config.PUSHES = config.PUSHES + 1


def coin_event():
    """Registers a coin insertion event
    """
    config.LASTIMPULSE = time.time()
    config.PULSES = config.PULSES + 1


def button_pushed():
    """Actions button pushes by number
    """
    print("Push button: ", config.PUSHES, " times")
    logger.info("Call function button_pushed with pushes: ")
    logger.info(config.PUSHES)
    
    if config.PUSHES == 1 or config.FIAT > 0:
        """If no coins inserted, update the screen.
        If coins inserted, scan a qr code for the exchange amount
        """
        
        # Clarify if exception FIAT > 0 was TRUE => set pulses 1
        if config.PUSHES > 1:
            config.PUSHES = 1
            logger.info("Restriction for the button => Set pulses = 1")

        # If no wallet is configured
        if not config.conf["atm"]["activewallet"]:
            logger.error("No wallet has been configured for the ATM.")
            logger.error("Please configure your Lightning Wallet first.")
            # "no wallet setup" message
            display.update_wallet_fault()
            time.sleep(5)

            # Softreset and startup screen
            softreset()
            return

        # If no FIAT has been deposited yet
        if config.FIAT == 0:
            display.update_nocoin_screen()
            time.sleep(3)
            display.update_startup_screen()
            config.PUSHES = 0
            return

        lnurlproxy = config.conf["lnurl"]["lnurlproxy"]
        activewallet = config.conf["atm"]["activewallet"]
        camera = config.conf["atm"]["camera"]
        # Determine if LNURL Withdrawls are possible
        if lnurlproxy == "active" or activewallet == "lnbits":
            # 1. Ask if wallet supports LNURL, if camera available
            # 2. Offer to cancel and switch to normal scan
            # 3. Process payment
            if activewallet == "lnbits" and camera == True:
                display.update_lnurl_cancel_notice()
                time.sleep(5)
                if config.PUSHES == 1:
                    # Process LNURL
                    logger.info("LNURL process stared")
                    lntxbot.process_using_lnurl(config.SATS)
                    softreset()
                    return
                if config.PUSHES > 1:
                    # Process QR code scan
                    logger.info("QR scan process started")
                    display.update_qr_request()
                    config.INVOICE = qr.scan_attempts(4)
                    display.update_payout_screen()
                    lntxbot.payout(config.SATS, config.INVOICE)
                    softreset()
                    return

            # If no camera is available, process LNURL directly
            if activewallet == "lnbits":
                # Process LNURL
                logger.info("LNURL process stared")
                
                # lnbits invoice or lnurlw?
                if config.conf["lnbits"]["method"] == "invoice":
                    while config.INVOICE is False:
                        display.update_qr_failed()
                        time.sleep(1)
                        display.update_qr_request()
                        qrcode = qr.scan()
                        config.INVOICE = lnbits.evaluate_scan(qrcode)
                    display.update_payout_screen()
                    lnbits.handle_invoice()
                    softreset()
                    return
                elif config.conf["lnbits"]["method"] == "lnurlw":
                    # Process LNURL
                    import requests
                    resp = lnbits.create_lnurlw()
                    qr_img = utils.generate_lnurl_qr(resp["lnurl"])
                    # TODO Adjust size according to screen used
                    qr_img = qr_img.resize((122, 122), resample=0)

                    # draw the qr code on the e-ink screen
                    display.draw_lnurl_qr(qr_img)
                    success = lnbits.wait_for_lnurlw_redemption(resp["id"], timeout=int(config.conf["lnbits"].get("timeout", 90)))
                    if success:
                        pass
                    else:
                        pass # some feedback for the user would be cool!
                    softreset()
                    return
                else:
                    logger.error("Invalid method defined for LNbits: " + config.conf['lnbits'].get('method'))
                    softreset()
                    return
                
                softreset()
                return
            
            if lnurlproxy == "active":
                display.update_lnurl_cancel_notice()
                time.sleep(5)
                if config.PUSHES == 1:
                    # Process LNURL
                    # Only implemented for LND BTCPay and Blink so far
                    import requests, json, qrcode

                    request_url = config.conf["lnurl"]["lnurlproxyurl"]
                    data = {"amount": config.SATS}

                    response = requests.post(request_url, json=data)

                    qr_img = utils.generate_lnurl_qr(response.json()["lnurl"])
                    # TODO Adjust size according to screen used
                    qr_img = qr_img.resize((122, 122), resample=0)

                    # draw the qr code on the e-ink screen
                    display.draw_lnurl_qr(qr_img)
                    invoice = requests.get(response.json()["callback"])

                    config.INVOICE = invoice.json()["invoice"]
                    if activewallet == "btcpay":
                        lndrest.handle_invoice()
                    elif activewallet == "blink":
                        blink.handle_invoice()
                    softreset()
                    return
                if config.PUSHES > 1:
                    # Process QR code scan
                    # Only implemented for LND BTCPay and Blink so far
                    display.update_qr_request()
                    qrcode = qr.scan()
                    config.INVOICE = lndrest.evaluate_scan(qrcode)
                    while config.INVOICE is False:
                        display.update_qr_failed()
                        time.sleep(1)
                        display.update_qr_request()
                        qrcode = qr.scan()
                        config.INVOICE = lndrest.evaluate_scan(qrcode)
                    display.update_payout_screen()
                    if activewallet == "btcpay":
                        lndrest.handle_invoice()
                    elif activewallet == "blink":
                        blink.handle_invoice()
                    softreset()
                    return
        elif config.conf["atm"]["activewallet"] == "btcpay_lnd":
            # Process QR code scan
            # Only implemented for LND BTCPay so far
            logger.info("No option for LNURL. Continue with scan...")
            display.update_qr_request()
            qrcode = qr.scan()
            config.INVOICE = lndrest.evaluate_scan(qrcode)
            while config.INVOICE is False:
                display.update_qr_failed()
                time.sleep(1)
                display.update_qr_request()
                qrcode = qr.scan()
                config.INVOICE = lndrest.evaluate_scan(qrcode)
            display.update_payout_screen()
            lndrest.handle_invoice()
            softreset()
            return
        else:
            logger.error("No valid wallet configured")

    if config.PUSHES == 9:
        """Reset Wallet and Scan new wallet credentials
        """
        logger.info("Wallet reset and new scan (9 times button)")
        
        # Delete current wallet flag and credentials
        config.update_config("atm", "activewallet", "")
        config.update_config("lntxbot", "creds", "")
        config.update_config("lnd", "macaroon", "")

        display.update_wallet_scan()
        qr.scan_credentials()
        importlib.reload(config)

        if config.conf["atm"]["activewallet"] == "btcpay_lnd":
            display.update_btcpay_lnd()
        elif config.conf["atm"]["activewallet"] == "lntxbot":
            balance = lntxbot.get_lnurl_balance()
            display.update_lntxbot_balance(balance)
        else:
            logger.error("Saving of wallet credentials failed.")

        softreset()

    if config.PUSHES == 3:
        """Simulates adding a coin (for testing)
        """
        logger.info("Simulate coin for test with pulses (3 times button)")
        print("Simulate coin for test with pulses (3 times button)")
        config.PULSES = 2
        config.PUSHES = 0
        return

    if config.PUSHES == 7:
        """Shutdown the host machine
        """
        display.update_shutdown_screen()
        logger.warning("ATM shutdown (7 times button)")
        os.system("sudo shutdown -h now")

    if config.PUSHES == 5:
        """Show all displays once
        """
        logger.info("Show all displays once (5 times button)")

        print("1. display.error_screen(message=ERROR)")
        display.error_screen(message="ERROR")
        time.sleep(2)

        print("2. display.update_qr_request()")
        display.update_qr_request()
        time.sleep(2)

        print("3. display.update_qr_failed()")
        display.update_qr_failed()
        time.sleep(2)

        print("4. display.update_payout_screen()")
        display.update_payout_screen()
        time.sleep(2)

        print("5. display.update_payment_failed()")
        display.update_payment_failed()
        time.sleep(2)

        print("6. display.update_thankyou_screen()")
        display.update_thankyou_screen()
        time.sleep(2)

        print("7. display.update_nocoin_screen()")
        display.update_nocoin_screen()
        time.sleep(2)

        print("8. display.update_lnurl_generation()")
        display.update_lnurl_generation()
        time.sleep(2)

        print("9. display.update_shutdown_screen()")
        display.update_shutdown_screen()
        time.sleep(2)

        print("10. display.update_wallet_scan()")
        display.update_wallet_scan()
        time.sleep(2)

        print("11. display.update_lntxbot_balance(balance)")
        display.update_lntxbot_balance(123)
        time.sleep(2)

        print("12. display.update_btcpay_lnd()")
        display.update_btcpay_lnd()
        time.sleep(2)

        print("13. display.draw_lnurl_qr(qr_img)")
        qrImage = Image.new('1', (122, 122), 255)
        display.draw_lnurl_qr(qrImage)
        time.sleep(2)

        print("14. display.update_amount_screen()")
        display.update_amount_screen()
        time.sleep(2)

        print("15. display.update_lnurl_cancel_notice()")
        display.update_lnurl_cancel_notice()
        time.sleep(2)

        print("16. display.update_button_fault()")
        display.update_button_fault()
        time.sleep(2)

        print("17. display.update_wallet_fault()")
        display.update_wallet_fault()
        time.sleep(2)

        print("18. display.update_startup_screen()")
        display.update_startup_screen()
        time.sleep(2)

        print("That's it, have fun!")

        config.PUSHES = 0
        return

    else:
        # If pushes not defined
        logger.info("Show pushes not defined  (x times button)")
        display.update_button_fault()
        time.sleep(3)
        display.update_startup_screen()

    # Reset pulses
    config.PUSHES = 0


def coins_inserted():
    """Actions coins inserted
    """
    
    print("Coin pulses: ", config.PULSES, " pulses")

    # Intercept and display a loose contact
    if config.PULSES == 1:
        print("Ups.. Just one coin pulses is not allowed!")
        logger.error("Ups.. Just one coin pulses is not allowed!")
        config.PULSES = 0
        return

    # Check if we should update prices
    if config.FIAT == 0:
        # Our counter is 0, meaning we got no fiat in:
        config.BTCPRICE = utils.get_btc_price(config.conf["atm"]["cur"])
        config.SATPRICE = (1 / (config.BTCPRICE * 100)) * 1e8
        logger.debug("Satoshi price updated")

    # We must have gotten pulses!
    config.FIAT +=      float(config.COINTYPES[config.PULSES]['fiat'])
    config.COINCOUNT += 1
    config.SATS =       utils.get_sats()
    config.SATSFEE =    utils.get_sats_with_fee()
    config.SATS -=      config.SATSFEE
    logger.info("Added {}".format(config.COINTYPES[config.PULSES]['name']))
    display.update_amount_screen()

    # Coin was processed -> Release coin acceptor relay switch
    lockout_relay.on()

    # Reset pulse cointer
    config.PULSES = 0

    if config.FIAT > 0 and not button_led.value == 1:
        # Turn on the LED after first coin
        button_led.on()
        logger.debug("Button-LED turned on (if connected)")


def monitor_coins_and_button():
    """Monitors coins inserted and buttons pushed
    """
    
    # 200 ms sleep for CPU idle and other processes
    time.sleep(0.1)
    # Too long a delay will have a negative effect on the coin detection and the lockout relay

    #Wifi monitoring causes undesirable behavior sometimes.
    #ssid=check_connectivity()
    #print(ssid)
    #if not ssid:
    #    # We are not connected!
    #    config.CONNECTIVITY=False
    #    display.error_screen("No connectivity")
    #    logger.error("No connectivity")
    #    time.sleep(5)
    #    return False
    #else:
    #    if not config.CONNECTIVITY:
    #        # We have an SSID now but not before
    #        config.CONNECTIVITY=True
    #        display.update_startup_screen()
    #        return False

    # Detect when coins are being inserted
    if (time.time() - config.LASTIMPULSE > 0.3) and (config.PULSES > 0):
        # New Coin to process -> Relay switch to inhibit
        lockout_relay.off()
        coins_inserted()

    # Detect if the button has been pushed
    if (time.time() - config.LASTPUSHES > 1) and (config.PUSHES > 0):
        # Pulses from push button -> Relay switch to inhibit
        if not config.PUSHES == 3:
            lockout_relay.off()
        button_pushed()

    # Processing pulses finish -> Release coin acceptor relay switch
    lockout_relay.on()

    # Automatic payout if specified in config file
    if (int(config.conf["atm"]["payoutdelay"]) > 0) and (config.FIAT > 0):
        if time.time() - config.LASTIMPULSE > int(config.conf["atm"]["payoutdelay"]):
            config.PUSHES = config.PUSHES + 1


# def check_dangermode():
#     """Check for DANGERMODE and wipe any saved credentials if off"
#     """
#     # if dangermode is NOT on
#     if config.conf["atm"]["dangermode"].lower() != "on":
#         logger.warning("DANGERMODE off")
#
#         # wipe any saved values from the config by saving an empty value to it
#         config.update_config("lntxbot", "creds", "")
#         config.update_config("lnd", "macaroon", "")
#         config.update_config("atm", "activewallet", "")
#
#         # get the static dict from within the conf and overwrite it to config.conf
#         config.conf = config.conf._sections
#
#         # get new lntxbot creds from qr code scan
#         print("Scan lntxbot creds now\n")
#         print("            +---+")
#         print("+-----------+---+")
#         print("|      .-.      |")
#         print("|     (   )     |")
#         print("|      `-'      |")
#         print("+---------------+\n")
#         time.sleep(2)
#         try:
#             config.conf["lntxbot"]["creds"] = lntxbot.scan_creds()
#             logger.info("Credentials saved in volatile memory (deleted after reboot)")
#         except utils.ScanError:
#             logger.error("Error scanning lntxbot creds with dangermode off")
#             return
#     else:
#         logger.info("DANGERMODE on. Loading values from config.ini...")
#         # config.check_config()


def main():
    utils.check_epd_size()
    logger.info("Application started")
    print("Application started")

    # Checks dangermode and start scanning for credentials
    # Only activate once software ready for it
    # check_dangermode()

    # Display startup info
    display.update_shutdown_screen()
    button_led.on()
    time.sleep(1)

    # Display startup startup_screen
    display.update_startup_screen()
    button_led.off()

    # Function call by rising/falling new signal
    button_signal.when_pressed = button_event
    coin_signal.when_released = coin_event

    while True:
        monitor_coins_and_button()


if __name__ == "__main__":
    while True:
        try:
            main()
        except KeyboardInterrupt:
            display.update_shutdown_screen()
            logger.info("Application finished (Keyboard Interrupt)")
            sys.exit(" Manually Interrupted")
        except Exception:
            logger.exception("Oh no, something bad happened! Restarting...")
            os.execv("/home/pi/LightningATM/app.py", [""])

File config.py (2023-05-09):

from configparser import ConfigParser
from shutil import copyfile
import logging
import math
import sys
import os

import utils

home = os.path.expanduser("~")
ATM_data_dir = home + "/.lightningATM/"
config_file_path = ATM_data_dir + "config.ini"
# check the config directory exists, create it if not
if not os.path.exists(ATM_data_dir):
    os.makedirs(ATM_data_dir)

# Set to logging.DEBUG if more info needed
logging.disable(logging.DEBUG)

# Set to logging.DEBUG if more "requests" debugging info needed
logging.getLogger("requests").setLevel(logging.INFO)
logging.getLogger("urllib3.connectionpool").setLevel(logging.INFO)

# Configure basigConfig for the "logging" module
logging.basicConfig(
    filename="{}/debug.log".format(ATM_data_dir),
    format="%(asctime)-23s %(name)-9s %(levelname)-7s | %(message)s",
    datefmt="%Y/%m/%d %I:%M:%S %p",
    level=logging.DEBUG,
)

# Create logger for this config file
logger = logging.getLogger("CONFIG")


yes = ["yes", "ye", "y"]
no = ["no", "n"]


def ask_scan_config_val(section, variable):
    while True:
        try:
            res = input(
                "Do you want to scan to input {} {}".format(section, variable)
            ).lower()
            if res in yes:
                # value = scan the qr for the value
                # update_config(section, variable, value
                ...
            elif res in no:
                return
            else:
                print("Input invalid, please try again or KeyboardInterrupt to exit")
        except KeyboardInterrupt:
            return


def check_config():
    """Checks the config and prompt the user to provide values for missing keys
    """
    if conf["lnd"]["macaroon"] is (None or ""):
        logger.warning("Missing value for lnd macaroon in config")
        ask_scan_config_val("lnd", "macaroon")
    if conf["lntxbot"]["creds"] is (None or ""):
        logger.warning("Missing value for lntxbot credential in config")
        ask_scan_config_val("lntxbot", "creds")


def update_config(section, variable, value):
    """Update the config with the new value for the variable.
    If dangermode is on, we save them to config.ini, else we write them to the temporary
    dictionary
    """
    if conf["atm"]["dangermode"].lower() == "on":
        config = create_config()
        config[section][variable] = value

        with open(CONFIG_FILE, "w") as configfile:
            config.write(configfile)
    else:
        conf[section][variable] = value


def check_dangermode():
    if conf["atm"]["dangermode"].lower() == "on":
        return True
    else:
        return False


# config file handling
def get_config_file():
    # check that the config file exists, if not copy over the example_config
    if not os.path.exists(ATM_data_dir + "config.ini"):
        example_config = os.path.join(os.path.dirname(__file__), "example_config.ini")
        copyfile(example_config, ATM_data_dir + "config.ini")
    return os.environ.get("CONFIG_FILE", config_file_path)


def create_config(config_file=None):
    parser = ConfigParser(comment_prefixes="/", allow_no_value=True, strict=False)
    parser.read(config_file or CONFIG_FILE)
    return parser


CONFIG_FILE = get_config_file()
conf = create_config()

######################################################
### (Do not change any of these parameters unless  ###
### you know exactly what you are doing.           ###
######################################################

# TODO: Add variable to set certificate check to true or false

# Papirus eInk size is 128 x 96 pixels
WHITE = 1
BLACK = 0
PAPIRUSROT = 0
if "papirus" in conf["atm"]["display"]:
    try:
        from papirus import Papirus
        PAPIRUS = Papirus(rotation=PAPIRUSROT)
    except ImportError:
        logger.warning("Papirus display library not installed.")
        print("Papirus library not installed.")
        sys.exit("Exiting...")

# Display - Waveshare 2.13 V2 is 250 * 122 pixels
elif "waveshare2in13v2" in conf["atm"]["display"]:
    try:
        from waveshare_epd import epd2in13_V2
        WAVESHARE = epd2in13_V2.EPD()
    except ImportError:
        logger.warning("Waveshare display library not installed.")
        print("Waveshare2in13v2 library not installed.")
        sys.exit("Exiting...")

# Display - Waveshare 2.13 V3 is 250 * 122 pixels
elif "waveshare2in13v3" in conf["atm"]["display"]:
    try:
        from waveshare_epd import epd2in13_V3
        WAVESHARE = epd2in13_V3.EPD()
    except ImportError:
        logger.warning("Waveshare display library not installed.")
        print("Waveshare2in13v3 library not installed.")
        sys.exit("Exiting...")

# Display - Waveshare 2.13 (D) is 212 * 104 pixels
elif "waveshare2in13d" in conf["atm"]["display"]:
    try:
        from waveshare_epd import epd2in13d
        WAVESHARE = epd2in13d.EPD()
    except ImportError:
        logger.warning("Waveshare display library not installed.")
        print("Waveshare2in13d library not installed.")
        sys.exit("Exiting...")

# Display - Waveshare 2.66 is 296 * 152 pixels
elif "waveshare2in66" in conf["atm"]["display"]:
    try:
        from waveshare_epd import epd2in66
        WAVESHARE = epd2in66.EPD()
    except ImportError:
        logger.warning("Waveshare display library not installed.")
        print("Waveshare2in66 library not installed.")
        sys.exit("Exiting...")

# Display - Waveshare 2.7 is 264 * 176 pixels
elif "waveshare2in7" in conf["atm"]["display"]:
    try:
        from waveshare_epd import epd2in7
        WAVESHARE = epd2in7.EPD()
    except ImportError:
        logger.warning("Waveshare display library not installed.")
        print("Waveshare2in7 library not installed.")
        sys.exit("Exiting...")

# Display - Waveshare 2.9 (D) is 296 * 128 pixels
elif "waveshare2in9d" in conf["atm"]["display"]:
    try:
        from waveshare_epd import epd2in9d
        WAVESHARE = epd2in9d.EPD()
    except ImportError:
        logger.warning("Waveshare display library not installed.")
        print("Waveshare2in9d library not installed.")
        sys.exit("Exiting...")

# Display - Inky pHAT
elif "inkyphat" in conf["atm"]["display"]:
    try:
        from inky.auto import auto

        WHITE = 0
        BLACK = 1
        INKY = auto(ask_user=True, verbose=True)
        INKY.set_border(INKY.WHITE)
    except ImportError:
        logger.warning("Inky display library not installed.")
        print("Inkyphat library not installed.")
        sys.exit("Exiting...")

# This could help for testing purposes (e.g. tests/lnbits_lnurlw.py)
elif "testing" in conf["atm"]["display"]:
    logger.warning("Display is in testing mode. This won't work in production.")

# Display - No configuration match
else:
    logger.warning("No display configuration match.")
    print("No display configuration matched.")
    sys.exit("Exiting...")

# API URL for coingecko
COINGECKO_URL_BASE = "https://api.coingecko.com/api/v3/"
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

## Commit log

2019-08-30 test with buttons
2019-09-05 add reset mode for buttons
    [app.py]
2019-09-05 fix payment request api
    [lightning.py]
2019-09-07 add utils, coin acceptor, button
2019-09-13 add qr scan failed message
    [display.py]
2019-09-13 repeat qr scan if failed
    [app.py]
2019-09-20 add payment failed message
    [display.py]
2019-09-20 display json error response
    [lightning.py]
2019-09-20 add message about turned off device
2019-10-24 add LightningATM on stage pictures
2019-10-24 add restart/shutdown button
2019-10-25 add box laser cut
    [box_layout.dxf]
2019-10-25 add box without labels
    [box_layout_without_labels.dxf]
2019-10-25 add assembly rendering
2019-10-26 add RaspberryPi Zero 3d model
    [RaspberryPiZeroW.STEP, RaspberryPiZeroW.STL]
2019-10-26 add dxf laser template
    [LightningATM - Sketch.dxf]
2019-10-27 add more 3d resources
    [LightningATM - Sketch 2.dxf]
2019-10-28 add final laser layout
    [LightningATM - Sketch - final laser layout.dxf]
2019-11-01 add final laser cut
    [#LightningATM - Sketch - final laser layout.dxf]
2019-11-08 add lnurl request (two times button push)
2019-11-28 Fix debug.log and accessing dangermode and lntxbot creds from config
    [app.py, config.py]
2019-11-28 Resolve dangermode yes/no on/off
    [app.py, config.py]
2019-11-28 Fix input lntxbot creds
    [app.py, lightning.py, lntxbot.py]
2019-11-29 Better error handling for lntxbot
    [lntxbot.py, qr.py, utils.py]
2019-11-29 renaming variables, remove print()
2019-12-13 rework to utilise qr.scan()
    [lntxbot.py]
2019-12-17 add outer and inner compartment designs
    [innerbox.dxf, outerbox.dxf]
2019-12-17 add compartemets for camera
    [Compartments.dxf]
2019-12-18 add laser cut dxf
    [LightningATM - New - Acrylic.dxf, LightningATM - New - Engraving.dxf, LightningATM - New - MDF.dxf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]
2019-12-19 add additional DXF files
    [RoundedBox.dxf, bend_pattern.dxf]
2019-12-20 upload newest dxf files
    [#LightningATM - Sketch - final laser layout.dxf, LightningATM - V0.1 - final laser layout.dxf, LightningATM - V0.1.dxf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]
2020-01-29 change to 3d files
    [#LightningATM - V0.3 - ATM.dxf]
2020-02-08 update small changes
    [#LightningATM - V0.3 - ATM.dxf, LightningATM - V0.3 - ATM.dxf]
2020-02-09 add function for button-led
2020-04-04 utils: Use requests instead of pycoingecko
    LighningATM needs only one simple GET requests to CoinGecko API for
    getting the Bitcoin price. Installing an additional library for that not
    necessary, requests can be used instead.
    Fixes: #13
    [utils.py]
2020-04-08 move URL to due import errors
    [config.py]
2020-04-09 remove custom error class
    [utils.py]
2020-05-01 library fix, error message fix
    [app.py]
2020-07-07 missing fee calc for 100 cents
    [app.py]
2020-07-11 add option for payoutdelay rather than button
2020-07-15 remove raspipi 3d files
    [RaspberryPiZeroW.STEP, RaspberryPiZeroW.STL]
2020-07-15 remove old dxf files
    [LightningATM - V0.1 - final laser layout.dxf, LightningATM - V0.1.dxf, LightningATM - V0.2 - Acrylic.dxf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]
2020-07-15 rearrange dxf files into different folders
    [LightningATM - V0.1 - final laser layout.dxf, LightningATM - V0.1.dxf, LightningATM - V0.2 - Acrylic.dxf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]
2020-07-16 remove 1mm option
    [LightningATM - V0.4 - MDF - 1mm (optional).dxf, LightningATM - V0.4 - MDF - 3mm.dxf]
2020-07-17 Add acrylic laser cut
    [LightningATM Pocket Edition - V0.1 - Acrylic - 3mm.dxf]
2020-07-29 bugfix in dxf
    [LightningATM - V0.3 - ATM.dxf, LightningATM - V0.3 - Compartments.dxf]
2020-08-18 update 3mm acrylic dxf
    [LightningATM Pocket Edition - V0.1 - Acrylic - 3mm.dxf]
2020-08-18 upload atm pocket edition dxf
    [LightningATM Pocket Edition - V0.1 - Engraving.dxf, LightningATM Pocket Edition - V0.1 - MDF - 3mm.dxf]
2020-08-25 black and white fix
    [config.py]
2020-10-19 add 3d print files Pocket Case
    [Back_Lid_NORMAL_v1_NoSupp.stl, Back_Lid_THICKER_v1_NoSupp.stl, Front_Glass_v1_NoSupp.stl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]
2021-03-28 catch missing library errors
    [config.py]
2021-03-28 fix lntxbot payout method without lnurl
    [app.py, lntxbot.py]
2021-07-25 BUG: LNURL authentication fails - log entry
    Bugfix: If authentication for LNURL fails, an error is logged and app continues.
    [lntxbot.py]
2021-07-29 Messages translated in de - german by WOLF64
2021-08-29 CHG: Adjustment of the text alignment in the display BUG: Replace displayPartial call, because it doesn't work. BUG: Replace displayPartBaseImage call, because it crashes, it doesn't exist in the dri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
2021-11-01 CHG: Fix exclusive configuration of a single display after merge
    [config.py]
2021-11-19 New option for Waveshare 2.66 display
    ADD: Display: Waveshare 2.66
    BUG: Fix unknown FULL_UPDATE and PART_UPDATE
    BUG: Fix unknown displayPartBaseImage and displayPartial
    CHG: Adjusting the text alignment and text size
    [config.py]
2021-12-07 BUG: Fixes a bug in related with pulses and the quick insertion of coins An adjustment is required so that coins can be inserted more quickly
    [app.py]
2022-01-21 BUG: An error when selecting the display has been fixed There could be ambiguity when using waveshare2in13 or waveshare2in13d displays. This is fixed by unique names now.
    [config.py]
2022-02-17 Revision of the documentation (#56)
    Detailed instructions how to assemble the atm and bring it into operation.
2022-03-14 DOC: Create an RPi image from scratch
    Guide that creates an image from scratch with the current RPi version "Bullseye".
2022-03-14 MRG: Update button functionality
    * Bug Fix 1: The "No coins added! Please add coins first" was invoked on a key press and then invoked alternately with the start screen without stopping. With this fix, the page is only called once.
    * Bug Fix 2: The "GPIO.add_event_detect" function is used for the GPIO.BCM input 5 and 6. These processes then run in the background parallel to the main program. These processes must also be stopped again if the program is ended with "except KeyboardInterrupt" , otherwise there will be overlaps and the bouncing phenomenon during a soft start.
    * Changed the order of button actions so that the severity of the action is increasing. The "wallet reset" is fatal and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
    [app.py, button_test.py]
2022-03-29 Update display functions and documentation
    * Added two new display messages
    * Extension by two display pages
    * Add display test function
    * set mulitiligual
    * update button.md
    * Add we_need_you_help.md
2022-03-29 GPIO change and lockout relay for coin acceptor
    * Replaced RPi.GPIO with GPIO Zero
    * Documentation edited
    * Edit messages
    [app.py, button_test.py]
2022-03-30 Correction of help side
    * Update of documentation
    [app.py]
2022-03-30 Makes camera function optional
    Expands the config.ini by asking whether a camera is available
2022-04-24 DOC: Insert Waveshare 2.13 V3 information
2022-04-24 DOC: Insert notice about required ssh connection
2022-05-20 ADD: Magnet case version
    [Case Magnet.stl, Front Magnet.stl, Logo Backplate Magnet.stl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]
2022-07-04 CHG: Reactivation of time.sleep for CPU idle
    * Reactivation of time.sleep for CPU idle
    ** 200 ms delay for CPU idle and other processes
    ** Too long a delay will have a negative effect on the coin detection and the lockout relay
    * Update time.sleep(0.1)
    ** Set CPU sleep time to 0,1 second. CPU workload then is 15%, thats fine. 0,2 s would be 10% and 0,01 would be 25-30%. Nothing would be 100%.
    [app.py]
2023-05-21 Update docu for lnbits api
    Add help page for LNbits Wallet
    Add display test picture und possible error and solution
2023-07-24 CHG: Fixed timeout when using lnbits
    [app.py, lnbits.py]
2023-10-30 ADD: Magnet case
    Added magnet Case version and created a Info text file, with links where to buy the magnets.
